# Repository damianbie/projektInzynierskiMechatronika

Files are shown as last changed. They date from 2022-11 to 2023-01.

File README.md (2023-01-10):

# Projekt Inżynierski z Mechatroniki

## struktura katalogów

- raport - raport projektu
- algorytm - implementacją algorytmu A i środowiska testowewgo
- robot - projekt fizycznego rogota
    - cady - proejkt cad robota
    - pcbV2 - projekt płytki w programie kiCad
    - soft - oprogramowanie robota napisane w C++ i IDF4.4

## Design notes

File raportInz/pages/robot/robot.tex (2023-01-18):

\section{Projekt robota}
\subsection{Założenia projektowe}
Wykonany robot powinien być jak najmniejszy i najprostszy w wykonaniu oraz sterowaniu tak aby móc przetestować przy jego pomocy działanie algorytmu A*. 
Robot będzie zbudowany z platformy, do której zostaną przyczepione napędy, elektronika sterująca oraz bateria. 
Do platformy zostaną przymocowane dwa gotowe moduły napędowe składające się z silnika, przekładni oraz dużego koła. 
Aby pojazd stał stabilnie, doczepione zostanie trzecie koło obracające się swobodnie w każdym kierunku.
Całość będzie sterowana przy pomocy mikroprocesora ESP32 oraz dwukanałowego sterownika silników DC opartym na układzie L298n.
Za zasilanie będzie odpowiadał litowo-jonowy akumulator 4S.

\subsection{Projektowanie robota w środowisku CAD}
Podstawa robota utrzymująca wszystkie komponenty zostanie wydrukowana na drukarce 3D, a
model platformy i pozostałych posiadanych elementów został wykonany w programie Fusion 360.
Wykonane modele modułów napędowych, przedniego kółka oraz baterii pozwoliły na optymalne rozmieszczenie wszystkich elementów.

\begin{figure}[H]
	\centering
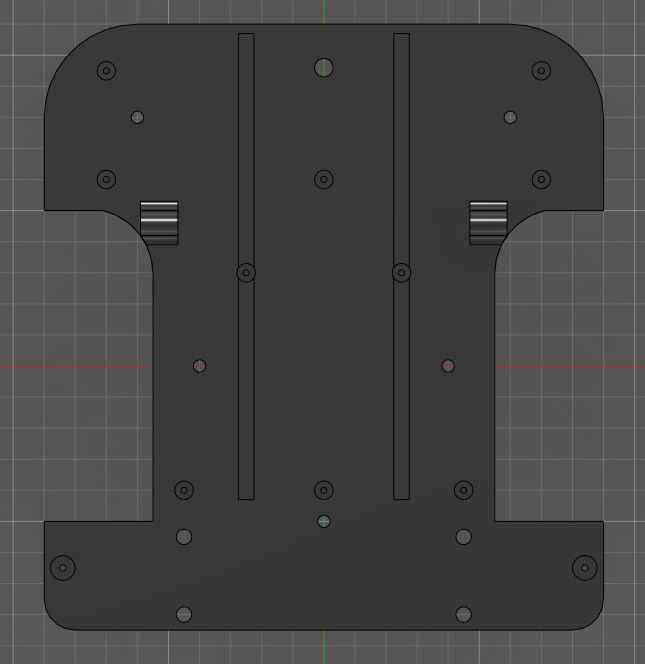
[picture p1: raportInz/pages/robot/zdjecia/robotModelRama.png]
	
	\caption{Widok z góry na podwozie robota}
	\label{Fig:robotModelRama}
\end{figure}

Model został przygotowany w programie Ultimaker Cura i wydrukowany z filamentu PLA.
Temperatur głowicy wynosiła 220$ ^\circ C$ a stołu 60$ ^\circ C$. Aby przyśpieszyć wydruk, wysokość warstwy została ustawiona na 0,2mm. 
Żeby zwiększyć wytrzymałość i lepiej zgrzać warstwy, temperatura głowicy została lekko zawyżona względem wymagań producenta filamentu,
a model posiada dwa dodatkowe wsporniki wzdłuż platformy.

\begin{figure}[H]
	\centering
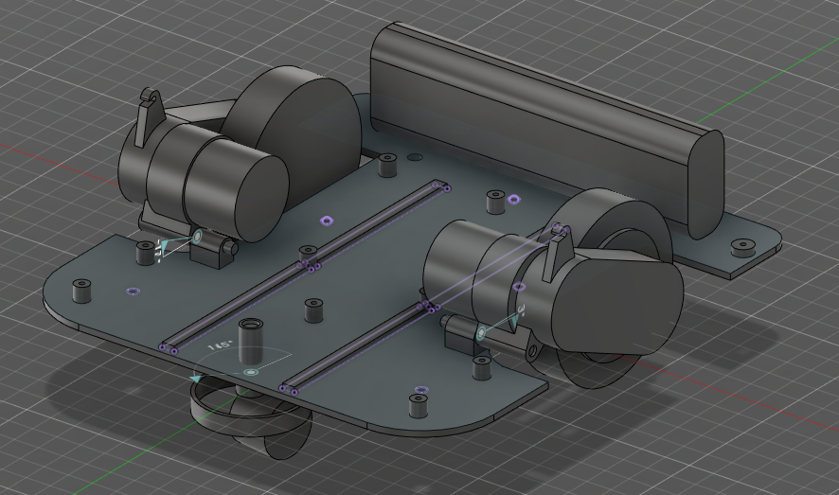
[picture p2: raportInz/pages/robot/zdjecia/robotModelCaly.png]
	
	\caption{Model robota z modułami}
	\label{fig:robotModelCaly}
\end{figure}

Na powyższym zdjęciu widać zaprojektowaną ramę wraz z odpowiednio ustawionymi gotowymi modułami. 
Moduły napędowe zaczepione są przy pomocy fabrycznego trzpienia wciskanego w ramę. 
Takie rozwiązanie oznacza że napęd może obracać się w wokół własnej osi. Aby zapewnić stały i równomierny docisk koła do podłoża,
napęd został połączony sprężyną z ramą. 

\subsection{Elektronika sterująca robotem}
Do bezprzewodowego sterowania robotem zostanie wykorzystany moduł ESP32, dla którego zostanie przygotowana odpowiednia płytka 
z wyprowadzeniami do enkoderów silnika oraz ich sterownika. Schemat i projekt płytki drukowanej został wykonany w programie KiCad. 
\begin{figure}[H]
	\centering
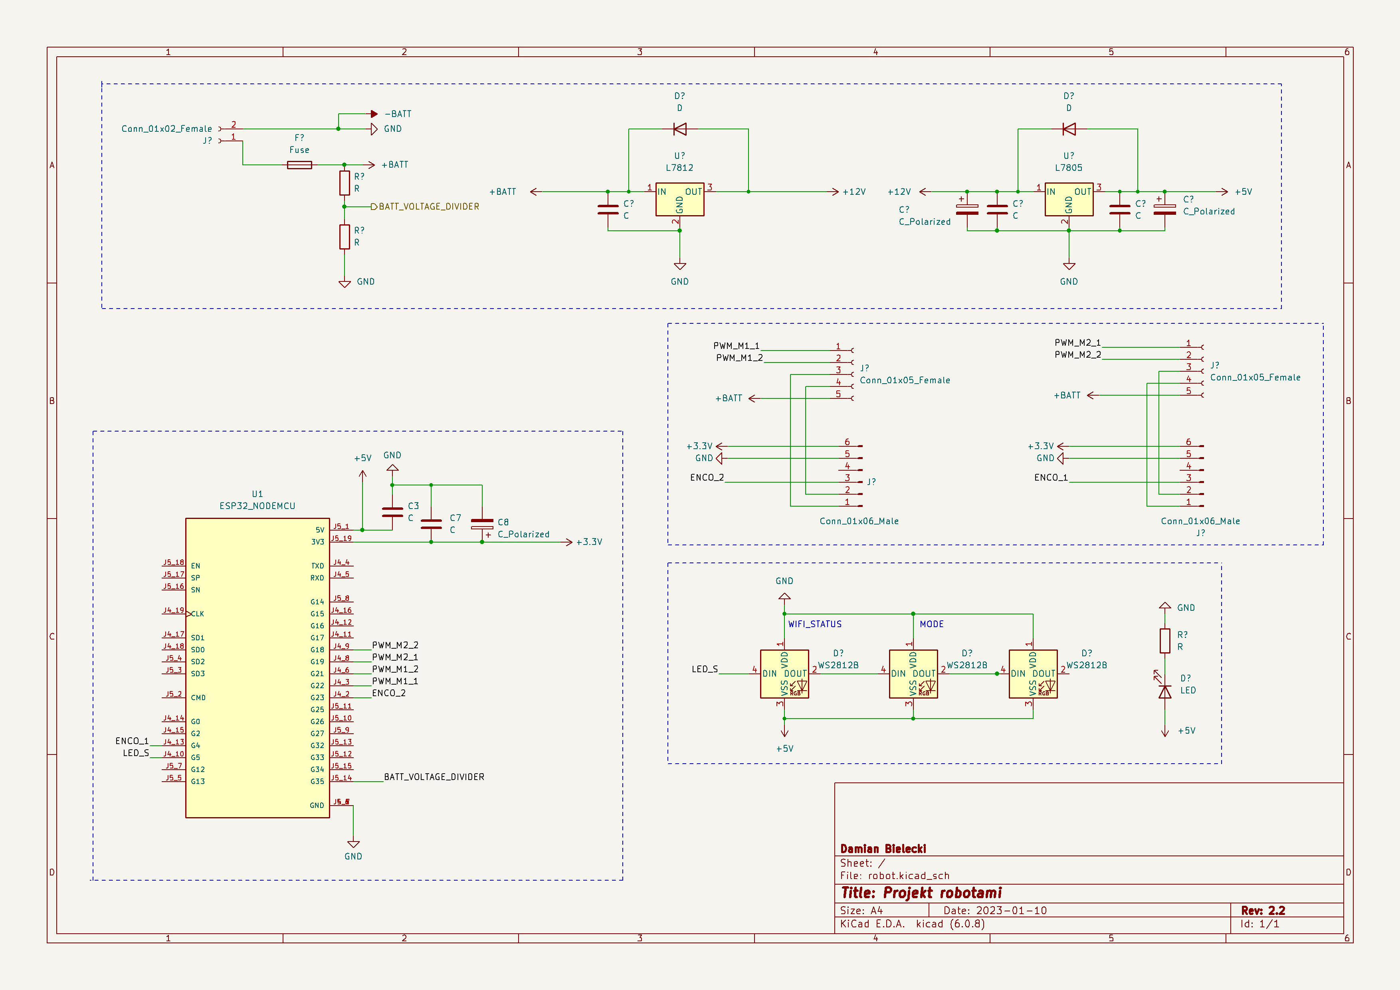
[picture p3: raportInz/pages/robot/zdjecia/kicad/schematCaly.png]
	
	\caption{Schemat połączeń pomiędzy modułami}
	\label{Fig:schematKiCad}
\end{figure}

Przedstawiony powyżej schemat został podzielony na kilka sekcji. 
Najbardziej rozbudowana jest sekcja zasilania, która poprzez dwa stabilizatory liniowe obniża napięcie z 16,8V do 5V. Mikroprocesor zasilany jest
napięciem 3,3V przygotowanym przez układ wlutowany na płytce deweloperskiej. Każda linia zasilania filtrowana jest przez kondensator elektrolityczny 
i ceramiczny, wynika to z dużego poboru prądu podczas komunikacji z WiFi. 

Kolejny segment zawiera po dwa złącza na silnik. Pierwsze złącze służy do połączenia z silnikiem, zasilania i odbierania danych z enkodera.
Drugie złącze służy do połączenia sterownika z silnikiem i dwoma kanałami PWM, pozwalającymi na płynne sterowanie kierunkiem i prędkością obrotową silnika.

Trzeci segment zawiera świecące diody programowalne służące do sygnalizacji stanu robota. Zaletą wykorzystanych tych diod jest szeregowe połączenie 
i bezpośrednie zasilanie z lini 5V. Ostatnia podłączona dioda jest na stałe i sygnalizuje podłączoną baterię.

Ostatnia sekcja, to połączenia pomiędzy modułem deweloperskim ESP32 a resztą układu. Mikroprocesor pracuje w logice 3,3V a sterownik silników 5V. 
Mimo tego, nie są potrzebne żadne układy zamieniające poziomy napięć. 
Dodatkowo obok wyprowadzeń modułu widać dodatkowe kondensatory filtrujące zasilanie. 
 
Użyte moduły napędowe posiadają enkoder inkrementalny zbudowany z czujnika halla i tarczy magnetycznej zamocowanej na wale silnika.
Silniki sterowane są modułem z układem L298n, a prędkość ustalana jest poprzez odpowiednio generowany sygnał PWM.
\begin{figure}[H]
	\centering
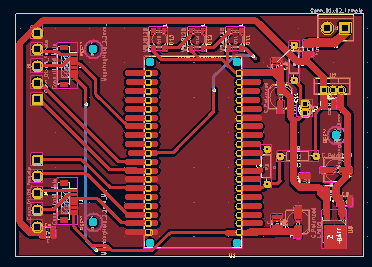
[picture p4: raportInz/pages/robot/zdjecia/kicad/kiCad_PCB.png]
	
	\caption{Projekt PCB}
	\label{Fig:kiCadPCB}
\end{figure}

Na widocznym powyżej zdjęciu widać ostateczną wersje płytki drukowanej. Większość połączeń na płytce zrealizowana jest poprzez górną warstwę miedzi,
jednak widać kilka ścieżek w dolnej warstwie.

\begin{figure}[H]
	\centering
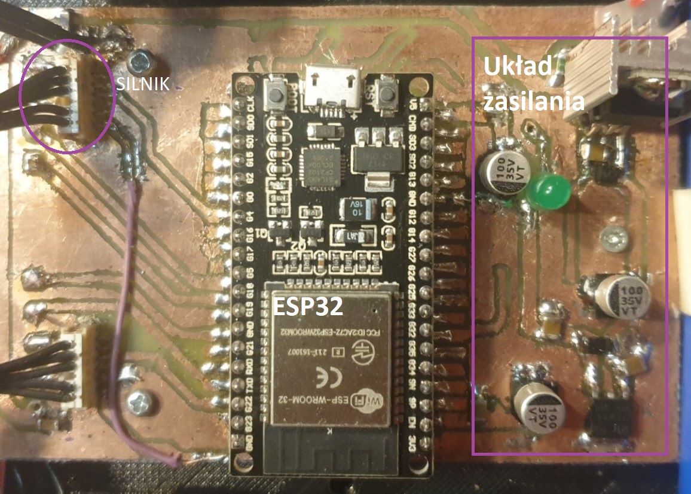
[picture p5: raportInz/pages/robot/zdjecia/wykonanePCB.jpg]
	
	\caption{Wykonana płytka}
	\label{Fig:wykonanePCB}
\end{figure}

Płytka została wykonana na jednostronnym laminacie poprzez naniesienie utwardzalnej światłem UV maski. Pozostała nie utwardzona część maski 
została zmyta w roztworze węglanu sodu. Tak przygotowana płytka została wytrawiona w 40\% roztworze chlorku żelaza(|||). 
Połączenia na dolnej warstwie zostały wykonane przy pomocy dodatkowych kabli. 

\begin{figure}[H]
	\centering
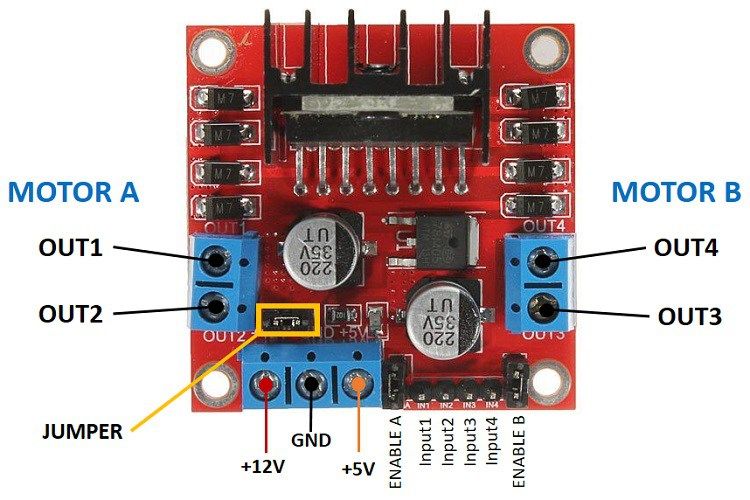
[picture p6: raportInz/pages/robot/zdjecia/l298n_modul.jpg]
	
	\caption{Wykorzystany moduł do sterowania silnikami}
	\label{Fig:modulL298}
\end{figure}

Wykonana płytka połączona jest z zewnętrznym dwukanałowym sterownikiem silników opartym na układzie L298n. 
Sterownik maksymalnie może obsłużyć silniki do 46V i 2A. Jego dużą zaletą jest praca w 5V logice
oraz zabezpieczenie przed niedozwolonymi stanami i nadmierną temperaturą. 

\subsection{Oprogramowanie robota}

Program sterujący robotem został napisany w C++,
a szkielet aplikacji bazuje na projekcie utworzonym przez framework IDF w wersji 4.4 udostępnionym 
przez producenta użytego procesora. Po za tym użyta została biblioteka implementująca 
system czasu rzeczywistego FreeRTOS i ASIO do obsługi połączenia TCP. 
\begin{figure}[H]
	\centering
	
	\caption{Schemat programu cz.1 }
	\label{Fig:Rysunek}
\end{figure}
\begin{figure}[H]
	\centering
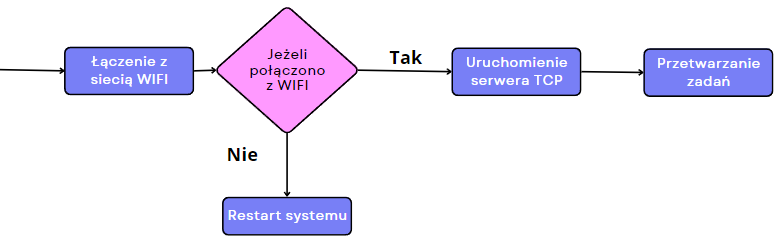
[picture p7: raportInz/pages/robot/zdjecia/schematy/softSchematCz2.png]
	
	\caption{Schemat programu cz.2}
	\label{Fig:Rysunek}
\end{figure}

Działanie programu rozpoczyna się od wywołania funkcji app\_main, inicjalizacji funkcji systemowych i sterowników silników.
W dalszej kolejności nawiązywana jest łączność z siecią WiFi. W przypadku braku połączenia system resetuje się. 
Po poprawnym połączeniu uruchamiany jest kontekst biblioteki ASIO, a następnie uruchomienie serwera TCP.
Klienci po połączeniu do utworzonego serwera wysyłają komendy tekstowe wraz z odpowiednimi argumentami, które
robot odpowiednio przetwarza. 

\subsubsection{Sterowanie silnikami}
Sterowanie silnikami odbywa się poprzez klasę MotorController, która dziedziczy po klasie PIDController implementującej regulator PID.
Obiekt automatycznie tworzy timer uruchamiający co 100ms metodę aktualizującą wyjścia sterujące silnikiem. 
Aktualna prędkość wyznaczana jest na podstawie przerwania wyzwalanego przez enkoder silnika. Przerwanie inkrementuje licznik, 
czyszczony przez wcześniej opisany timer. Nastawy regulatora PID zostały dobrane eksperymentalnie, człon proporcjonalny wynosi 8 a całkujący i różniczkujący 0,1. 
Regulator PID możemy opisać przy pomocy wzoru:

\begin{equation}
	u(x) = e(x) * P + \int{e(x)} * I + \partial{e(x)} * D 
	\label{Eq:PID}
\end{equation}
Gdzie: $e(x)$ -- jest błędem; P,I,D -- to stałe odpowiednio członu proporcjonalnego, całkującego i różniczkującego

\begin{equation}
	e(x) = y_{nast}(x) - y_{aktu}(x)
	\label{Eq:blad}
\end{equation}
Gdzie: $y_{nast}(x)$ -- to nastawa regulatora, $y_{aktu}(x)$ -- jest rzeczywistą zmierzoną wartością
 
Powyżej przedstawiony regulator został zaimplementowany w funkcji calcOutput klasy PIDController.

\begin{lstlisting}[language=C++,caption=Zaimplementowany w C++ regulator PID,label={kodCPPPIDOutput}]
float PIDController::calcOutput(float current, float set)
{
	float error = set - current;
	float der = (error - this->_lastValue)/(_timeStep* 0.001);
	
	float output =  (this->_p * error) + 
					(this->_i * error * this->_timeStep * 0.001) + 
					(this->_d * der);

	this->_lastValue = error;
	return output;
}
\end{lstlisting}

Do wyznaczenia części różniczkującej potrzebna jest wartość błędu z poprzedniego wywołania pętli, a ta zapisywana jest do zmiennej prywatnej klasy lastValue. 
Całkowanie zrealizowane jest poprzez pomnożenie przez krok dyskretyzacji. Stałe regulatora ustawiane są poprzez wywołanie konstruktora klasy.

Tak zaimplementowany regulator używany jest do wyznaczenia sygnału PWM, bezpośredniego sterującego układem L298n a ten silnikami. 

\begin{lstlisting}[language=C++,caption=Wyznaczenie modulacji PWM,label={kodCPPPWM}]
if(abs(setSpeed) - 1 > 0)
{
	pidToPwm = (int) this->calcOutput(abs(this->getCalculatedEngineRadialSpeed()), abs(setSpeed));
	if(setSpeed < 0)
	{
		pwmCh = 1;
	}
	else
		pwmCh = 0;

	pidToPwm += ledc_get_duty(LEDC_LOW_SPEED_MODE, this->_chanels[pwmCh]);
	pidToPwm = std::min(pidToPwm, 8192);
	pidToPwm = std::max(pidToPwm, 0);
}

// ustawienie wyjsc
ledc_set_duty(LEDC_LOW_SPEED_MODE, this->_chanels[pwmCh], (int)pidToPwm);
ledc_update_duty(LEDC_LOW_SPEED_MODE, this->_chanels[pwmCh]);

// ustawienie drugiego kanalu
ledc_set_duty(LEDC_LOW_SPEED_MODE, this->_chanels[(pwmCh==0)?1:0], 0);
ledc_update_duty(LEDC_LOW_SPEED_MODE, this->_chanels[(pwmCh==0)?1:0]);
\end{lstlisting}

W pierwszej kolejności sprawdzana jest zadana prędkość, jeżeli ta jest zbyt niska to na piny wystawiane są bezpośrednio stany niskie.
Jeżeli ustawiona prędkość jest poprawna to wyznaczamy wyjście regulatora. Sterowanie kierunkiem obrotów odbywa 
się poprzez znak zadanej prędkości a więc regulator otrzymuje wartości bezwzględne. 
Wyjście regulatora PID sumowane jest z aktualną nastawą. Wyjścia pwm skonfigurowane są z częstotliwością 5kHz i rozdzielczością 13bitów. 
Przed wysłaniem nastaw do kontrolera pwm, te są obcinane do obsługiwanych zakresów (tj. 0 - 8192).

\subsubsection{Serwer TCP}

Po podłączeniu zasilania i uruchomieniu systemu robot oczekuje na polecenia wysłane do robota poprzez protokół internetowy TCP. Serwer został napisany w oparciu o bibliotekę ASIO, pozwalającą na asynchroniczną obsługę wejścia i wyjścia (w tym sieci).
\begin{figure}[H]
	\centering
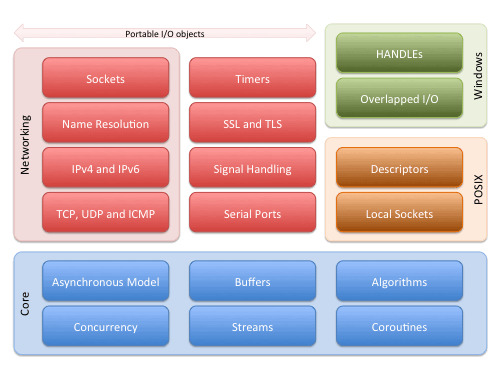
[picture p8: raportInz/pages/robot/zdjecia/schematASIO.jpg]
	
	\caption{Schemat biblioteki ASIO \cite{asio}}
	\label{Fig:schematASIO}
\end{figure}
Biblioteka została napisana w C++ i pracuje w oparciu o standard POSIX wspierany również przez wykorzystywane ESP32.
Do akceptacji przychodzących połączeń została napisana klasa Server. Konstruktor przyjmuję referencje do kontekstu utworzonego w funkcji głównej programu. 
Uruchomienie kontekstu jest ważną częścią biblioteki ASIO, przetwarzane są w niej wszystkie asynchroniczne operacje.
Aby zapewnić jak najlepszy czas przetwarzania, kontekst uruchomiony jest w oddzielnym wątku przyłączonym do drugiego fizycznego rdzenia.

\begin{figure}[H]
	\centering
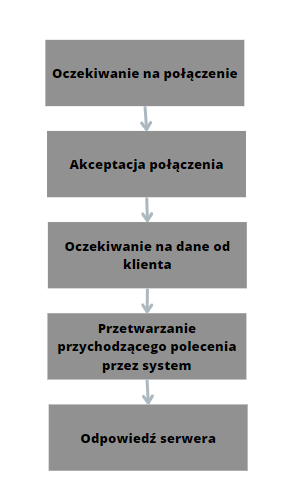
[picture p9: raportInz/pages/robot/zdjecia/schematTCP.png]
	
	\caption{Schemat działania serwera TCP}
	\label{Fig:schematSerweraTCP}
\end{figure}

Po zaakceptowaniu przychodzącego połączenia, obiekt połączenia dodawany jest do specjalnej tablicy przechowującej wszystkich klientów. 
Dane mogą być równocześnie przetwarzane w kilku miejscach a więc używane są dzielone wskaźniki, które automatycznie usuwają dane jeżeli nikt z nich nie korzysta.
Na każdym aktywnym połączeniu prowadzony jest nasłuch, dzięki czemu możemy mieć równocześnie podłączony program do generowania ścieżki i drugi pozwalający na podgląd parametrów robota.
Klient wysyła polecenia w formie tekstowej, te przekazywane są do klasy systemowej odpowiednio interpretujące ich przeznaczenie.
Jeżeli komenda tego wymaga (np. zwrócenie prędkości obrotowej silników) to dane są odsyłane do klienta w postaci tekstu i oddzielonych przerwą liczb. 

Należy pamiętać że podczas testowania i łączenia z różnymi sieciami, serwer dhcp będzie przydzielał różne adresy ip i należy to uwzględnić w programie łączącym się z robotem.

\textbf{Wykonany robot}

Poniżej widać zbudowanego i uruchomionego robota. Na zdjęciu możemy zauważyć że napęd został przyczepiony przy pomocy gumek, ponieważ 
oryginalne sprężyny tworzyły zbyt dużą siłę i robot stał krzywo. 

\begin{figure}[H]
	\centering
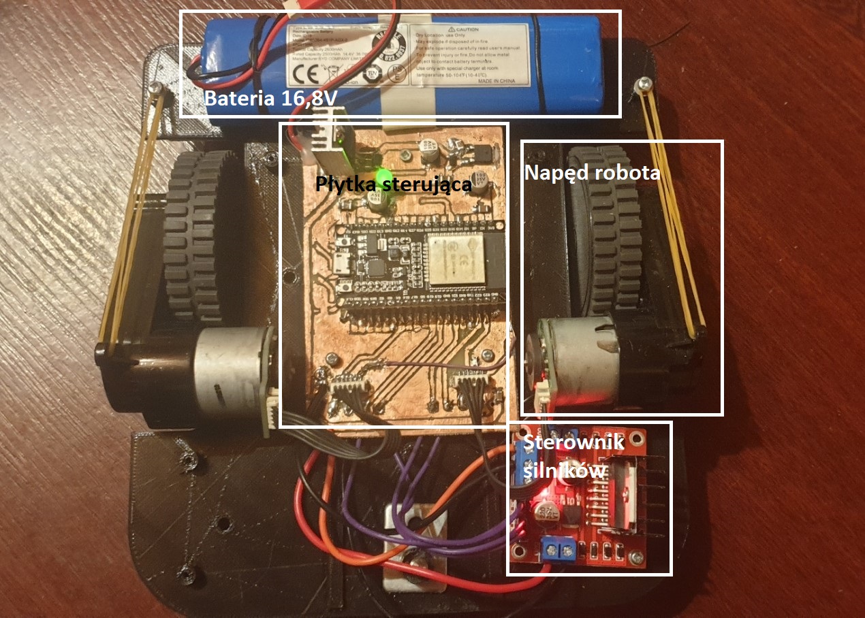
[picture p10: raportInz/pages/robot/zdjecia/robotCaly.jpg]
	
	\caption{Zbudowany robot}
	\label{Fig:zbudowanyRobot}
\end{figure}

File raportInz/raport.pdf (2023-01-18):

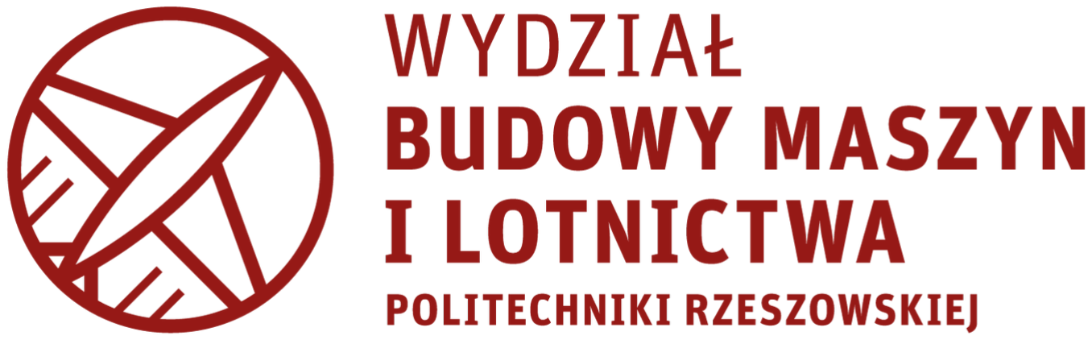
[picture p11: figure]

## Damian Bielecki

## Implementacja sterowania hierarchicznego mobilnym robotem kołowym z wykorzystaniem języka Python

## Praca dyplomowa inżynierska

## Opiekun pracy: dr inż. Paweł Penar

## Rzeszów, 2023

## Spis treści

## 1. Wprowadzenie

Od lat można zauważyć zwiększająca się popularność różnych robotów, które bazując na

wprowadzonej do systemu mapie autonomicznie poruszają się po terenie tak aby osiągnąć okre-

ślony cel. Celem projektu inżynierskiego będzie zaimplementowanie algorytmu wyszukującym

najkrótszą ścieżkę. Do przetestowania algorytmu zostanie napisany prosty program symulu-

jący robota poruszającego się po wyznaczonej ścieżce. Kolejnym etap projektu to zbudowanie

robota mającego zweryfikować zaproponowaną przez algorytm ścieżkę.

Głównym powodem podjęcia się implementacji takiego algorytmu jest chęć zapoznania

się z systemami planującymi ruch robota i próba zaimplementowania takiego rozwiązania na

fizycznym robocie.

Ze względu na cel projektu inżynierskiego oraz powód jego realizacji, przyjęto, że praca

będzie złożona z przeglądu literatury, implementacji i symulacji algorytmu A* w języku Python

oraz weryfikacji przyjętych rozwiązań obiekcie rzeczywistym.

Mając na uwadze zakres pracy, jej treść podzielono na szereg rozdziałów. Rozdział

pierwszy stanowi przegląd literatury oraz istniejących rozwiązań, które będą podstawą założeń

przyjętych we opracowywanym rozwiązaniu. Rozdział drugi skupia się na genezie, charakte-

rystyce i opisie działania wybranego algorytmu wyszukiwania najkrótszej ścieżki. Dodatkowo

zostaną przedstawione inne algorytmy zwiększającą autonomie robota mobilnego. Rozdział

trzeci przedstawia własną implementacje algorytmu A* oraz środowisko symulacyjne w języku

Python. Kolejny rozdział to omówienie budowy robota mobilnego oraz jego programu sterują-

cego. W tym kontekście szczególną uwagę poświęcono komunikacji oraz sterowaniu silnikami

Rozdział piąty stanowi podsumowanie pracy i przedstawia przeprowadzone testy wykonane w

środowisku symulacyjnym oraz rzeczywistym.

## 2. Przegląd literatury

### 2.1. Przegląd istniejących rozwiązań

Przeglądając dostępną literature opisującą algorytmy wyszukiwania najkrótszej ścieżki

możemy zauważyć pewien nie jawny podział. Pierwsza grupa artykułów skupia się na imple-

mentacji algorytmu, sprawdzeniu różnych funkcji heurestycznej i porównaniu szybkości wy-

znaczania trasy w zależności od liczby węzłów w mapie. Druga grupa artykułów przedstawia

bardziej ogólne zastosowania algorytmów takich jak A* w różnych dziedzinach przemysłu.

Pierwszy artykuł pt. "Path planning with modified A star algorithm for a mobile

robot"[1] przedstawia różne algorytmy do planowania ścieżki mobilnego robota, ich implemen-

tacje oraz przeprowadzone eksperymenty. Autorzy zwracają uwagę na to że roboty przede

wszystkim pracują wewnątrz budynków i mogą być zmuszone do budowania mapy środowiska

w trackie pracy przy pomocy metod SLAM. Do dynamicznej orientacji i generowania mapy

można wykorzystać istniejące projekty takie jak openSLAM[2] lub HectorSLAM[3] używanym

przez ROS. Jeżeli robot nie posiada żadnej mapy środowiska to musi bazować tylko i wyłącznie

na swoich wewnętrznych czujnikach co nazywa się nawigacją reaktywną. Do oceny algorytmów

wykorzystano kryteria takie jak: czas obliczeń, długość wygenerowanej ścieżki, liczbę odwie-

dzonych wierzchołków i symetrię badanego środowiska. Eksperymenty zostały przeprowadzone

w rzeczywistym środowisku i mapie wygenerowanej przez laserowy lidar robota przy pomocy

wcześniej wspomnianych metod SLAM. Z pierwszego podsumowania wynika że najlepszym

algorytmem jest JPS(A*), który jest najszybszy i odwiedził najmniej niepotrzebnych wierz-

chołków. Drugi najlepszy wynik miał 10x dłuższy czas wykonania i dotyczył niezmodyfikowa-

nej wersji algorytmu A*. Podsumowując wyniki eksperymentów najszybszym algorytmem był

JPS(A*) jednak ten wyznaczał dłuższe ścieżki. Autorzy zwracają uwagę że wybór algorytmu

zależy od tego czy wymagany jest mały czas obliczeń czy najkrótsza wyznaczona ścieżka.

Spora część artykułów skupia się na zaletach i potencjalnych różnych zastosowaniach

algorytmu A*. Jednym z nieoczywistych zastosowań wskazanych w analizowanych artykułach

jest przyśpieszenie analizy składniowej bez kontekstowych gramatyk probabilistycznych. W

przeciwieństwie do niektórych metod PCFG, algorytm A* zawsze zwróci drzewo o maksymal-

nym możliwym prawdopodobieństwie. [4]

Ponad to algorytm A* jest bardzo popularny w różnego rodzaju literaturze dotyczą-

cej gier komputerowych i sztucznej inteligencji. Dzięki niemu możemy w dosyć prosty sposób

określić ruch sztucznych obiektów w budowanej grze a dzięki prostocie i szybkości działania, algorytm nie będzie powodował dużego narzutu obliczeniowego na pozostały proces programu[5].

Ze względu na prostotę, jest często wykorzystywany w urządzeniach IOT, które mają

szczególne wymagania co do niskiego zużycia energi a więc cechują się niskimi osiągami pro-

cesora. Algorytm wykorzystywany jest między innymi w protokołach wyznaczających kolejne

routery w sieciach komputerowych[6]. Jednym z takich protokołów jest RIP, który wyznacza

trasę na podstawie wektora odległości.

### 2.2. Opis przyjętego rozwiązania

Algorytm wyznaczania najkrótszej ścieżki wraz z środowiskiem testowym został napi-

sany w języku Python. Implementacja algorytmu nie wymaga żadnych dodatkowych biblio-

tek. Do zbudowania środowiska symulacyjnego zostały użyte biblioteki graficzne do rysowania

kształtów geometrycznych oraz podstawowych elementów graficznego interfejsu użytkownika.

Weryfikacja działania algorytmu została przeprowadzona na zbudowanym trójkołowym robocie.

Oprogramowanie robota zostało napisane w języku C++ i dodatkowych bibliotekach udostęp-

nionych przez producentów użytych sterowników.

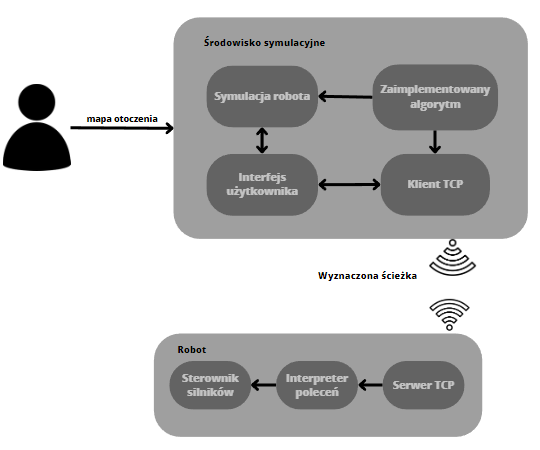
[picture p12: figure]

Rysunek 2.1: Ogólny schemat projektu

Użytkownik po uruchomieniu środowiska symulacyjnego będzie miał możliwość edycji

mapy opartej na siatce, określenia punktu początkowego i końcowego. Kolejnym krokiem jest

wyznaczenie ścieżki oraz jej graficznej reprezentacji. Tak wyznaczoną ścieżkę można wysłać do

robota operującego w środowisku rzeczywistym.

## 3. Algorytm A*

### 3.1. Geneza powstania

Algorytm A* powstał w ramach projektu Shakey, zapoczątkowanego w 1966 roku przez

Charles Rosen’a. Celem projektu było zbudowanie robota, który potrafiłby planować własne

działania. Zbudowany robot wyróżniał się na tle innych tym że integrował kilka różnych modeli

sztucznej inteligencji pracującej jako jeden system.

Robot został zbudowany z:

- kamery telewizyjnej i dalmierza optycznego - system wizyjny do obserwacji środowiska
- łącza radiowego - służącego do komunikacji z bazą, odbierania i wysyłania komend
- detektora uderzeń - pozwalający na zatrzymanie robota w przypadku kolizji

Komunikacja odbywała się poprzez wysyłane radiowo, tekstowe polecenia mające okre-

śloną strukturę np.: GOTO D4 - co oznaczało automatyczne przemieszczenie się robota do

wskazanej pozycji

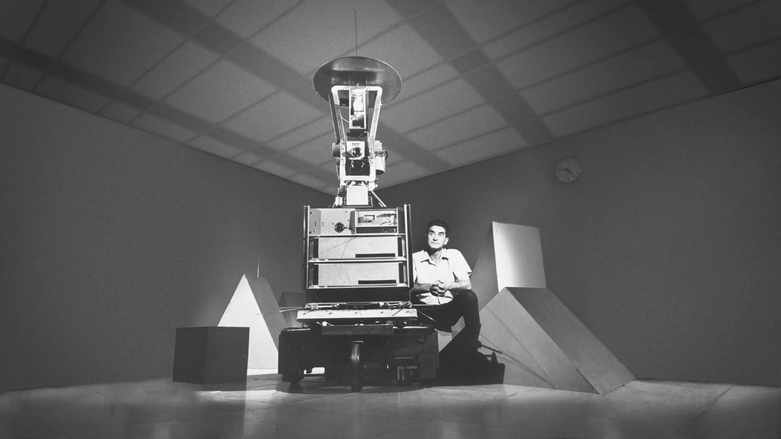
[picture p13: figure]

Rysunek 3.2: Robot Shakey i Charles Rosen, inicjator projektu [8]

### 3.2. Opis działania algorytmu

A* to heurestyczny algorytm wyznaczający najkrótszą możliwą ścieżkę w grafie. Jest to

algorytm zupełny i optymalny, a więc zawsze zostanie wyznaczone optymalne rozwiązanie. Ze względu na przeszukiwanie oparte na grafie algorytm działa najlepiej na strukturze drzewiastej.

Zadaniem algorytmu jest minimalizacja funkcji:

f(x) = h(x) +g(x) | (3.1)

gdzie: f(x) - minimalizowana funkcja, g(x) - to rzeczywisty koszt dojścia do punktu x.

Funkcja h(x) to funkcja heurestyczna, oszacowuje ona koszt dotarcia od punktu x do

wierzchołka docelowego

Zalety:

- jest kompletny i optymalny
- może przeszukiwać skomplikowane mapy
- jest najwydajniejszym takim algorytmem

Wady:

- jego wydajność w znacznej mierze zależy od funkcji heurestycznej
- Każda akcja ma stały koszt wykonania
- nie nadaje się do często zmieniającego się otoczenia robota, wymaga ponownego przeli-

czenia

Przykładowe funkcje heurestyczne:

- Funkcja euklidesowa

h(x) = K ∗

2

q
(x1 −x2)

2 + (y1 −y2)

2
(3.2)
- Geometria Manhattanu (inaczej metryka miejska)
h(x) = |x2 −x1|+|y2 −y1| | (3.3)
- Odległość oktylowa

h(x) = D1 ∗ (|x1 −x2|+|y1 −y2|) + (D2−2 ∗ D1) ∗min(|x1 −x2|,|y1 −y2|) (3.4)

Gdzie: x1 i y1 to współrzędne wyznaczanego punktu, x2 i y2 to koordynaty celu, K - oznacza

wzmocnienie, D1 - koszt skoku na wprost, D2 - koszt skoku po przekątnej

### 3.3. Analiza innych algorytmów

- RRT(Rapidly-exploring random tree)[12] - to algorytm generujący i łączący losowe

punkty w przestrzeni. Z każdym wygenerowanym wierzchołkiem sprawdzane jest czy

ten omija przeszkody. a jego działanie kończy się gdy wygenerowany węzeł jest we

wskazanym regionie lub zostanie osiągnięty limit. Jego zalety to:

- Balans pomiędzy zachłannością a eksploracją
- prosty i szybki w implementacji
- Zbiega się z rozkładem próbkowania

wady:

- jest czuły na metrykę
- duża złożoność obliczeniowa
- SLAM(Simultaneous localization and mapping) [13] - jest metodą używaną w

autonomicznych pojazdach. Pozwana na zbudowanie oraz lokalizacje pojazdu względem

otoczenia na mapie. Algorytm ten nie wyznacza bezpośrednio ścieżki omijającej prze-

szkody jednak w praktyce jest ważnym elementem takiego systemu. Każdy ruch robota

w rzeczywistym środowisku jak i sama mapa obarczona jest pewnym błędem powodują-

cym że robot znajduje się w innym miejscu niż zakładamy. Możemy wyróżnić działanie

algorytmu w oparciu o lidary albo o metody wizyjne. Wadą metody jest wysoki koszt

obliczeniowy i narastający z czasem błąd pozycji co w konsekwencji może spowodować

utratę pozycji.

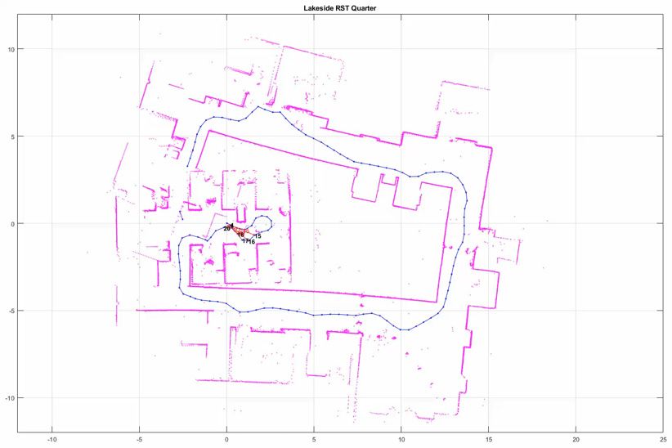
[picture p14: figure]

Rysunek 3.3: Przykład mapowania metodą SLAM[13]

## 4. Implementacja

### 4.1. Implementacja algorytmu

Mechanizm wyszukiwania najkrótszej ścieżki został zamknięty w jednym module o na-

zwie aStar. Na moduł składa się klasa AStar ze wszystkimi potrzebnymi metodami oraz do-

datkowa klasa Node reprezentująca pojedynczy punkt przeszukiwanego grafu.

Wyznaczanie najkrótszej ścieżki rozpoczyna się od wyznaczenia kosztu punktu starto-

wego i utworzenia zbioru z nieprzeszukanymi wierzchołkami, do którego dopisujemy punkt

początkowy.

1 | openList = []
2 | startNode . h = self . heurestic ( startNode . getCords () , endNode . getCords
() )
3 | startNode . g = 0
4 | heappush ( openList , startNode )

Listing 1: Przygotowanie danych

Wewnętrzna funkcja heurestic przyjmująca pozycje dwóch punktów odpowiada za wyli-

czenie optymistycznego kosztu przejścia od punktu x do wierzchołka docelowego. Takie podej-

ście pozwala na szybką podmianę funkcji bez znaczących zmian w programie. Wykorzystywana

funkcja heurestyczna to równanie nr. (3.2)

W kolejnym kroku uruchamiana jest pętla, która wykonywana jest dopóki w zbiorze

otwartym znajdują się nie odwiedzone elementy. Z listy pobierany jest element o najmniejszej

liczbie punktów co oznacza, że dany wierzchołek drzewa ma największe szanse być najlepszym

rozwiązaniem. Jeżeli pobrany element nie jest celem to dalej pobierani i przetwarzani są wszy-

scy jego sąsiedzi. W tym rozwiązaniu, dla zaoszczędzenia pamięci, symulator przechowuję tylko

przeszkody. W związku z tym do pobrania sąsiadów używana jest specjalna funkcja sprawdza-

jąca czy na mapie o wskazanych koordynatach istnieje punkt. Jeżeli takowy obiekt nie istnieje

to oznacza, że algorytm może użyć tych współrzędnych do trasowania ścieżki. Od tej części

programu zależy, czy algorytm ma wyznaczyć ścieżkę uwzględniając skoki po skosie.

1 | neighborNode = self . _findNodeOnList ( openList , newCords )
2 | if neighborNode is None :
3 | neighborNode = Node ( newCords )
4 | neighborNode . g = COST
5 | neighborNode . h = self . heurestic ( newCords , endNode . getCords () )
6 | neighborNode . parent = currentNode
7 | openList . append ( neighborNode )

8
9 | distance_from_curr_to_neighbor = COST
10 | scoreFromStartToCurrentNeighbor = | currentNode . g +
| distance_from_curr_to_neighbor

12 | if neighborNode . getScore () <= currentNode . getScore () :
13 | neighborNode . g = scoreFromStartToCurrentNeighbor
14 | neighborNode . h = scoreFromStartToCurrentNeighbor + self . heurestic (
| newCords , endNode . getCords () )
15 | neighborNode . parent = currentNode

Listing 2: Wyznaczenie kosztu ścieżki

Powyższy kod odpowiada za wyznaczenie kosztu przejścia do sąsiada. Jeżeli punkt nie

istnieje jeszcze w otwartym zbiorze to jest tworzony i do niego dodawany. Zgodnie z założeniem

całkowity koszt to suma rzeczywistego kosztu dystansu i wyniku funkcji heurestycznej. Rze-

czywisty koszt (funkcja g(x)) jest ustalony na sztywno i zależy od współrzędnych, do których

skaczemy. Jeżeli następny punkt jest na wprost to koszt wynosi 10. Jako iż przechodzimy po

siatce z węzłami o stałej i równej odległości to koszt skoku do sąsiada po skosie został wyzna-

czony z twierdzenia Pitagorasa. Należy zwrócić uwagę, że jeżeli całkowity koszt jest mniejszy

od aktualnego to węzeł ma ustawianego rodzica, ma to duże znaczenie w przypadku wyjścia z

pętli i wyznaczenia najkrótszej trasy spośród wszystkich kosztów.

1 | if currentNode == endNode :
2 | path = []
3 | while currentNode is not None :
4 | path . append ( currentNode )
5 | currentNode = currentNode . getParent ()
6 | return path
7 | else :
8 | return []

Listing 3: Przygotowanie danych

Po zakończeniu pętli, sprawdzane jest czy została znaleziona ścieżka, jeżeli takowa ist-

nieje to w kolejnej pętli wyznaczane są przy pomocy pola wskazującego na rodzica kolejne

punkty trasy. Jeżeli węzeł nie jest punktem końcowym to trasa nie została znaleziona i zwra-

cana jest pusta lista.

### 4.2. Implementacja środowiska testowego

Środowisko symulacyjne zostało napisane w języku Python i bibliotekach pygame[9] i

pygame_gui[10], zapewniających obsługę graficznego interfejsu użytkownika.

1 | if __name__ == ’__main__ ’:
2 | app = App ()
3 | app . main ()

Listing 4: Uruchomienie aplikacji

Obsługa mapy

Dla logicznego podzielenia programu została napisana główna klasa programu o nazwie

App. Takie podejście pozwoliło na odseparowanie poszczególnych funkcji aplikacji. W pierwszej

kolejności konstruktor obiektu aplikacji, generuje okno, tworzy graficzne elementy użytkownika

oraz ustawia odpowiednie flagi informujące o stanie aplikacji. Dalej wywoływana jest funkcja

main wczytująca odpowiednią mapę z pliku, a następnie uruchamiająca główną pętlę programu

działającą w 60 klatkach na sekundę.

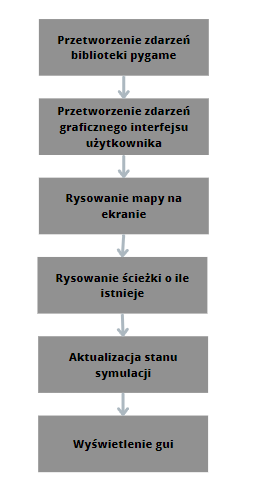
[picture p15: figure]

Rysunek 4.4: Schemat głównej pętli programu

Aby uprościć symulowanie różnych scenariuszy i rozmiarów map otoczenia, ta ładowana

jest ze wskazanego w programie pliku. Wskazany plik jest w formacie json i podzielony jest na

dwie sekcje. Pierwsza dostarcza informacji o samej mapie, natomiast druga o poruszającym się

po niej robocie. Sekcja mapy zawiera lokalizacje do pliku tekstowego z zapisanymi elementami.

1 ( self .map , self . robot ) = MapLoader . fromJson (" maps / m02 . json ")

Listing 5: Uruchomienie aplikacji

Ładowaniem wszystkich tych informacji zajmuje się specjalna metoda w klasie MapLoader,

wywołana przed uruchomieniem pętli głównej programu. Wczytywana mapa jest w postaci

siatki i każdy jej element ma stały rozmiar. Symulator rozróżnia kilka typów węzłów:

- brak elementu - możliwy przejazd
- ściana - przeszkoda do ominięcia przez algorytm
- punkt początkowy - od niego rozpoczyna się wyznaczanie ścieżki, jest zdefiniowany przez

użytkownika

- punkt końcowy - analogicznie jak w poprzednim przypadku
- ścieżka - element wyznaczonej trasy

Wszystkie wymienione typy zapisane są w klasie Tile, reprezentującej pojedynczy ry-

sowany i zapisywany w pliku kwadrat. Użytkownik może w każdej chwili działania aplikacji

edytować mapę a przed zamknięciem programu zaktualizowana mapa jest zapisywana do pliku.

Wyjątkiem jest obiekt będący elementem ścieżki, ten nie jest zapisywany do pliku, ponieważ

generowany jest dynamicznie i służy tylko do reprezentacji wygenerowanej ścieżki.

Wyznaczanie ścieżki i symulacja

Po załadowaniu program oczekuje na akcje użytkownika i ewentualne uruchomienie wy-

znaczania ścieżki lub całej symulacji.

1 | elif ev . ui_element == self . _startAStar :
2 | star = AStar ( self .map.map , self . map . getSize () )
3 | star . diagonalJump ( self . _diagonalJump )
4 | star . diagolnalCorrection ( self . _diagonalCorrextion )
5 | self . path | = star . findPath2 ( Node ( self . map . getStartCords () ) ,
Node (( self . map . getEndCords () ) ) )
6 | self . _pathExist = True
7 | self . robot . stopSimulation ()
8 | self . robot . hideRobot ()

Listing 6: Uruchomienie aplikacji

Po kliknięciu w przycisk odpowiadający za wyznaczenie i pokazanie ścieżki, program

tworzy obiekt wyznaczający trasę i ustawia dodatkowe opcje algorytmu (np. skok po przekąt-

nych). Dalej pobierana jest wyznaczona trasa będąca tablicą kolejnych punktów, po których

należy przejść aby dojść do celu. Na końcu ustawiana jest odpowiednia flaga programu, za-

trzymywana jest symulacja i ukrywany jest robot (mamy nowo wyznaczoną trasę). Przycisk

uruchamiający symulacje sprawdza czy istnieje ścieżka i w razie potrzeby ją generuje. Na-

stępnie trasa podawana jest do obiektu robota odpowiadającego za symulacje i dalej jest ona

uruchamiana.

Przejście robota po ścieżce

Symulator robota pobiera pierwszy punkt, do którego ma dotrzeć. Zmiana pozycji od-

bywa się poprzez regulator typu P z ustawioną nastawą na wskazany punkt. Wartość wzmoc-

nienia proporcjonalnego wczytana jest z pliku i oznaczona jest jako szybkość robota. Dalszy

etap to sprawdzenie czy symulowany robot dotarł do celu.

if abs ( deltaPos0 ) < 0.2 and abs ( deltaPos1 ) < 0.2:
self . _currentTarget -= 1

Listing 7: Uruchomienie aplikacji

Realizowane jest to poprzez sprawdzenie czy wartość bezwzględna z różnicy aktualnej oraz

docelowej pozycji jest mniejsza niż 0,1. Po osiągnięciu punktu, ustawiany jest nowy indeks

tablicy wskazujący na kolejny cel. Jeżeli na początku aktualizacji indeks jest ujemny to robot

przejechał po całej wyznaczonej trasie.

Komunikacja z robotem

Po wyznaczeniu ścieżki symulator na polecenie użytkownika może połączyć się ze zbudo-

wanym robotem aby ten osiągnął założony cel. Zgodnie ze schematem 2.1 robot po połączeniu

z siecią WiFi i utworzeniu serwera TCP oczekuje na wysyłane komendy. Aplikacja podczas

uruchamiania, tworzy gniazdo, które potem zostanie wykorzystane do połączenia.

1 | self . _robotSocket | = socket . socket ( socket . AF_INET , socket .
| SOCK_STREAM )

Listing 8: Utworzone gniazdo

Dla zwiększenia elastyczności utworzone zostały dwa pola tekstowe pozwalające na wprowa-

dzenie adresu ip oraz portu z uruchomionym serwerem. Po wprowadzeniu wymaganych danych

operator może spróbować nawiązać połączenie z robotem poprzez specjalny przycisk.

if self . _robotSocketFlag is True :
self . _robotSocket . close ()

print ( f" Laczenie z robotem {( self . _textRobotIp . get_text () , int( self . _textRobotPort . get_text ()))}")
self . _robotSocket . settimeout (1)
| try :
self . _robotSocket . connect (( self . _textRobotIp . get_text () , int ( self . _textRobotPort . get_text () ) ) )
self . _robotSocketFlag = True
self . _sendCommandToRobot (" setMode auto ")
print (" Podlaczono !!! ")
| except Exception as err :
self . _robotSocketFlag = False
print ( f" Blad polaczenia z robotem ")
| print ( err )

Listing 9: Nawiązanie połączenia

W pierwszej kolejności sprawdzana jest flaga informująca o stanie połączenia, jeżeli jest aktywne

to jest ono zamykane. Na utworzonym gnieździe wywoływana jest funkcja connect z wprowa-

dzonymi przez użytkownika parametrami. Cała operacja zamknięta jest w bloku try..except

a więc jeżeli program nie połączy się z robotem to wyświetlana jest odpowiednia informacja.

Podczas łączenia należy zwracać uwagę na podsieci, w których jest robot i sterujący laptop.

Dodatkowo robot posiada dynamiczne ip co zostało szerzej opisane w rozdziale o oprogramo-

waniu robota. Jeżeli żaden wyjątek nie został rzucony to wysyłana jest pierwsza komenda

ustawiająca tryb robota na automatyczny.

1 | def _sendCommandToRobot ( self , cmd ) :
2 | if self . _robotSocketFlag is False :
3 | print (" Robot nie podlaczony !!")
4 | return

5
6 | try :
7 | self . _robotSocket . send ( str . encode ( cmd ) )
8 | except OSError as err :
9 | print (" Robot nie podlaczony !!! ")
10 | self . _robotSocket . close ()
11 | self . _robotSocketFlag = False
12 | return

Listing 10: Wysyłanie komendy do robota

Program może wysłać dowolną komendę poprzez metodę sendCommandToRobot. Podobnie

jak przy połączeniu, metoda wysyłająca dane może rzucić wyjątek o braku połączenia. W

takim przypadku wyświetlana jest odpowiednia informacja i resetowana jest flaga połączenia.

Finalna wersja programu

Na poniższym zrzucie widać uruchomiony program z trwającą symulacją. Po prawej

stronie został umieszczony panel z interfejsem użytkownika. Po lewej stronie widoczna jest

wczytana mapa. Kolorem niebieskim został oznaczony punkt startowy a czerwonym końcowy.

Żółte kratki oznaczają wyznaczoną przez algorytm ścieżkę, po której przejdzie robot. Szare

pola to przeszkody, które robot ma ominąć. Robot oznaczony jest przez jasno-zielone koło,

które przesuwa się po mapie.

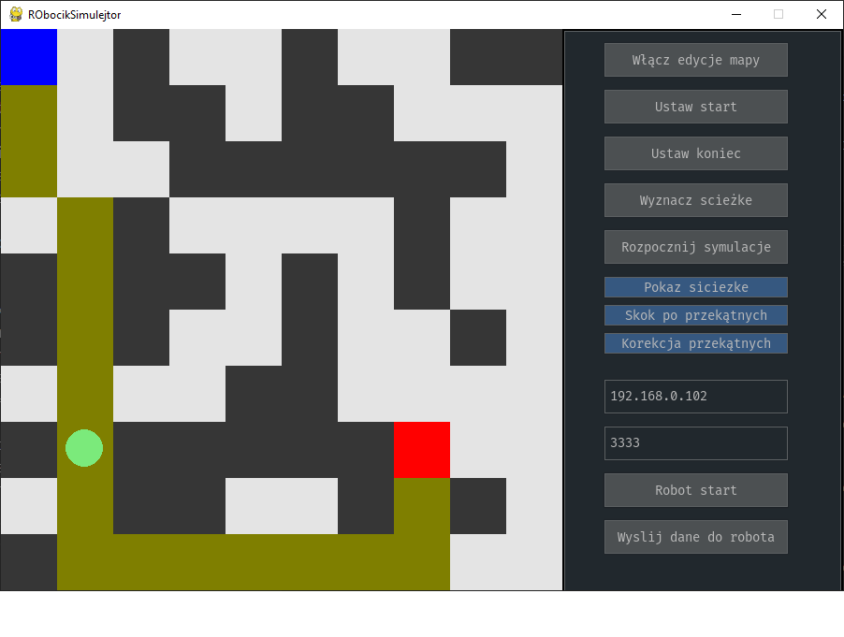
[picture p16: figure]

Rysunek 4.5: Widok finalnej wersji programu

## 5. Projekt robota

### 5.1. Założenia projektowe

Wykonany robot powinien być jak najmniejszy i najprostszy w wykonaniu oraz stero-

waniu tak aby móc przetestować przy jego pomocy działanie algorytmu A*. Robot będzie

zbudowany z platformy, do której zostaną przyczepione napędy, elektronika sterująca oraz ba-

teria. Do platformy zostaną przymocowane dwa gotowe moduły napędowe składające się z

silnika, przekładni oraz dużego koła. Aby pojazd stał stabilnie, doczepione zostanie trzecie

koło obracające się swobodnie w każdym kierunku. Całość będzie sterowana przy pomocy mi-

kroprocesora ESP32 oraz dwukanałowego sterownika silników DC opartym na układzie L298n.

Za zasilanie będzie odpowiadał litowo-jonowy akumulator 4S.

### 5.2. Projektowanie robota w środowisku CAD

Podstawa robota utrzymująca wszystkie komponenty zostanie wydrukowana na drukarce

3D, a model platformy i pozostałych posiadanych elementów został wykonany w programie

Fusion 360. Wykonane modele modułów napędowych, przedniego kółka oraz baterii pozwoliły

na optymalne rozmieszczenie wszystkich elementów.


Rysunek 5.6: Widok z góry na podwozie robota

Model został przygotowany w programie Ultimaker Cura i wydrukowany z filamentu

PLA. Temperatur głowicy wynosiła 220◦C a stołu 60◦C. Aby przyśpieszyć wydruk, wysokość

warstwy została ustawiona na 0,2mm. Żeby zwiększyć wytrzymałość i lepiej zgrzać warstwy, temperatura głowicy została lekko zawyżona względem wymagań producenta filamentu, a mo-

del posiada dwa dodatkowe wsporniki wzdłuż platformy.


Rysunek 5.7: Model robota z modułami

Na powyższym zdjęciu widać zaprojektowaną ramę wraz z odpowiednio ustawionymi

gotowymi modułami. Moduły napędowe zaczepione są przy pomocy fabrycznego trzpienia

wciskanego w ramę. Takie rozwiązanie oznacza że napęd może obracać się w wokół własnej osi.

Aby zapewnić stały i równomierny docisk koła do podłoża, napęd został połączony sprężyną z

ramą.

### 5.3. Elektronika sterująca robotem

Do bezprzewodowego sterowania robotem zostanie wykorzystany moduł ESP32, dla któ-

rego zostanie przygotowana odpowiednia płytka z wyprowadzeniami do enkoderów silnika oraz

ich sterownika. Schemat i projekt płytki drukowanej został wykonany w programie KiCad.


Rysunek 5.8: Schemat połączeń pomiędzy modułami

Przedstawiony powyżej schemat został podzielony na kilka sekcji. Najbardziej rozbu-

dowana jest sekcja zasilania, która poprzez dwa stabilizatory liniowe obniża napięcie z 16,8V

do 5V. Mikroprocesor zasilany jest napięciem 3,3V przygotowanym przez układ wlutowany na

płytce deweloperskiej. Każda linia zasilania filtrowana jest przez kondensator elektrolityczny i

ceramiczny, wynika to z dużego poboru prądu podczas komunikacji z WiFi.

Kolejny segment zawiera po dwa złącza na silnik. Pierwsze złącze służy do połączenia z

silnikiem, zasilania i odbierania danych z enkodera. Drugie złącze służy do połączenia sterow-

nika z silnikiem i dwoma kanałami PWM, pozwalającymi na płynne sterowanie kierunkiem i

prędkością obrotową silnika.

Trzeci segment zawiera świecące diody programowalne służące do sygnalizacji stanu

robota. Zaletą wykorzystanych tych diod jest szeregowe połączenie i bezpośrednie zasilanie z

lini 5V. Ostatnia podłączona dioda jest na stałe i sygnalizuje podłączoną baterię.

Ostatnia sekcja, to połączenia pomiędzy modułem deweloperskim ESP32 a resztą układu.

Mikroprocesor pracuje w logice 3,3V a sterownik silników 5V. Mimo tego, nie są potrzebne żadne układy zamieniające poziomy napięć. Dodatkowo obok wyprowadzeń modułu widać dodatkowe

kondensatory filtrujące zasilanie.

Użyte moduły napędowe posiadają enkoder inkrementalny zbudowany z czujnika halla

i tarczy magnetycznej zamocowanej na wale silnika. Silniki sterowane są modułem z układem

L298n, a prędkość ustalana jest poprzez odpowiednio generowany sygnał PWM.

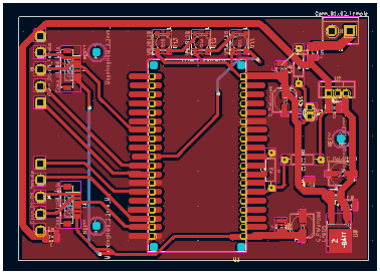
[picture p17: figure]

Rysunek 5.9: Projekt PCB

Na widocznym powyżej zdjęciu widać ostateczną wersje płytki drukowanej. Większość

połączeń na płytce zrealizowana jest poprzez górną warstwę miedzi, jednak widać kilka ścieżek

w dolnej warstwie.


Rysunek 5.10: Wykonana płytka

Płytka została wykonana na jednostronnym laminacie poprzez naniesienie utwardzalnej światłem UV maski. Pozostała nie utwardzona część maski została zmyta w roztworze wę-

glanu sodu. Tak przygotowana płytka została wytrawiona w 40% roztworze chlorku żelaza(|||).

Połączenia na dolnej warstwie zostały wykonane przy pomocy dodatkowych kabli.

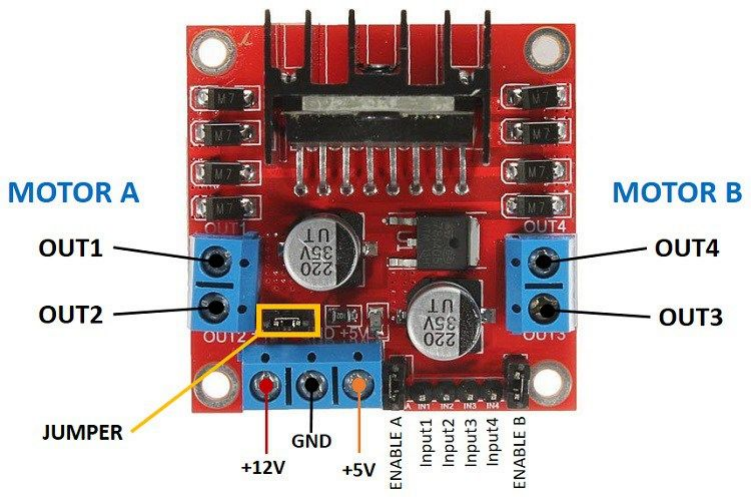
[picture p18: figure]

Rysunek 5.11: Wykorzystany moduł do sterowania silnikami

Wykonana płytka połączona jest z zewnętrznym dwukanałowym sterownikiem silników

opartym na układzie L298n. Sterownik maksymalnie może obsłużyć silniki do 46V i 2A. Jego

dużą zaletą jest praca w 5V logice oraz zabezpieczenie przed niedozwolonymi stanami i nad-

mierną temperaturą.

### 5.4. Oprogramowanie robota

Program sterujący robotem został napisany w C++, a szkielet aplikacji bazuje na pro-

jekcie utworzonym przez framework IDF w wersji 4.4 udostępnionym przez producenta użytego

procesora. Po za tym użyta została biblioteka implementująca system czasu rzeczywistego

FreeRTOS i ASIO do obsługi połączenia TCP.

Rysunek 5.12: Schemat programu cz.1

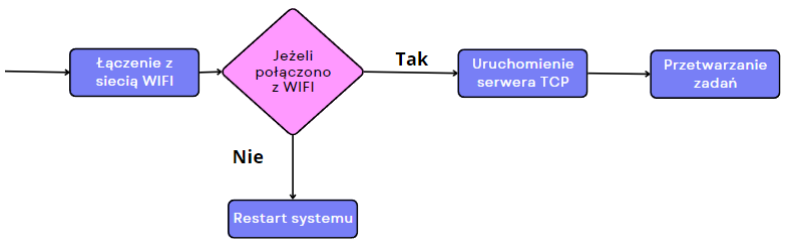
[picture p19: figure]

Rysunek 5.13: Schemat programu cz.2

Działanie programu rozpoczyna się od wywołania funkcji app_main, inicjalizacji funkcji

systemowych i sterowników silników. W dalszej kolejności nawiązywana jest łączność z siecią

WiFi. W przypadku braku połączenia system resetuje się. Po poprawnym połączeniu uru-

chamiany jest kontekst biblioteki ASIO, a następnie uruchomienie serwera TCP. Klienci po

połączeniu do utworzonego serwera wysyłają komendy tekstowe wraz z odpowiednimi argu-

mentami, które robot odpowiednio przetwarza.

### 5.4.1. Sterowanie silnikami

Sterowanie silnikami odbywa się poprzez klasę MotorController, która dziedziczy po

klasie PIDController implementującej regulator PID. Obiekt automatycznie tworzy timer uru-

chamiający co 100ms metodę aktualizującą wyjścia sterujące silnikiem. Aktualna prędkość

wyznaczana jest na podstawie przerwania wyzwalanego przez enkoder silnika. Przerwanie in-

krementuje licznik, czyszczony przez wcześniej opisany timer. Nastawy regulatora PID zostały

dobrane eksperymentalnie, człon proporcjonalny wynosi 8 a całkujący i różniczkujący 0,1. Re-

gulator PID możemy opisać przy pomocy wzoru:

u(x) = e(x) ∗P +

Z
e(x) ∗ I +∂e(x) ∗ D | (5.5)

Gdzie: e(x) – jest błędem; P,I,D – to stałe odpowiednio członu proporcjonalnego, całkującego

i różniczkującego

e(x) = ynast(x)−yaktu(x) | (5.6)

Gdzie: ynast(x) – to nastawa regulatora, yaktu(x) – jest rzeczywistą zmierzoną wartością

Powyżej przedstawiony regulator został zaimplementowany w funkcji calcOutput klasy

PIDController.

1 | float PIDController :: calcOutput ( float current , float set )
2 | {

3 | float error = set - current ;
4 | float der = ( error - this - > _lastValue ) /( _timeStep * 0.001) ;

5
6 | float output = | (this - > _p * error ) +
7 | (this -> _i * error * this - > _timeStep * 0.001) +
8 | (this -> _d * der ) ;

9
10 | this - > _lastValue = error ;
11 | return output ;
12 | }

Listing 11: Zaimplementowany w C++ regulator PID

Do wyznaczenia części różniczkującej potrzebna jest wartość błędu z poprzedniego wy-

wołania pętli, a ta zapisywana jest do zmiennej prywatnej klasy lastValue. Całkowanie zrealizo-

wane jest poprzez pomnożenie przez krok dyskretyzacji. Stałe regulatora ustawiane są poprzez

wywołanie konstruktora klasy.

Tak zaimplementowany regulator używany jest do wyznaczenia sygnału PWM, bezpo-

średniego sterującego układem L298n a ten silnikami.

1 | if( abs ( setSpeed ) - 1 > 0)
2 | {
3 | pidToPwm = ( int ) this - > calcOutput ( abs (this - >
getCalculatedEngineRadialSpeed () ) , abs ( setSpeed ) ) ;
4 | if( setSpeed < 0)
5 | {
6 | pwmCh = 1;
7 | }
8 | else
9 | pwmCh = 0;

10
11 | pidToPwm += ledc_get_duty ( LEDC_LOW_SPEED_MODE , this - > _chanels [ pwmCh ])
| ;
12 | pidToPwm = std :: min ( pidToPwm , 8192) ;
13 | pidToPwm = std :: max ( pidToPwm , 0) ;
14 | }

15
16 | // ustawienie wyjsc
17 | ledc_set_duty ( LEDC_LOW_SPEED_MODE , this - > _chanels [ pwmCh ] , (int) pidToPwm
) ;
18 ledc_update_duty ( LEDC_LOW_SPEED_MODE , this - > _chanels [ pwmCh ]) ;

19
20 | // ustawienie drugiego kanalu
21 | ledc_set_duty ( LEDC_LOW_SPEED_MODE , this - > _chanels [( pwmCh ==0) ?1:0] , 0) ;
22 | ledc_update_duty ( LEDC_LOW_SPEED_MODE , this - > _chanels [( pwmCh ==0) ?1:0]) ;

Listing 12: Wyznaczenie modulacji PWM

W pierwszej kolejności sprawdzana jest zadana prędkość, jeżeli ta jest zbyt niska to

na piny wystawiane są bezpośrednio stany niskie. Jeżeli ustawiona prędkość jest poprawna

to wyznaczamy wyjście regulatora. Sterowanie kierunkiem obrotów odbywa się poprzez znak

zadanej prędkości a więc regulator otrzymuje wartości bezwzględne. Wyjście regulatora PID sumowane jest z aktualną nastawą. Wyjścia pwm skonfigurowane są z częstotliwością 5kHz

i rozdzielczością 13bitów. Przed wysłaniem nastaw do kontrolera pwm, te są obcinane do

obsługiwanych zakresów (tj. 0 - 8192).

### 5.4.2. Serwer TCP

Po podłączeniu zasilania i uruchomieniu systemu robot oczekuje na polecenia wysłane

do robota poprzez protokół internetowy TCP. Serwer został napisany w oparciu o bibliotekę

ASIO, pozwalającą na asynchroniczną obsługę wejścia i wyjścia (w tym sieci).


Rysunek 5.14: Schemat biblioteki ASIO [11]

Biblioteka została napisana w C++ i pracuje w oparciu o standard POSIX wspierany

również przez wykorzystywane ESP32. Do akceptacji przychodzących połączeń została na-

pisana klasa Server. Konstruktor przyjmuję referencje do kontekstu utworzonego w funkcji

głównej programu. Uruchomienie kontekstu jest ważną częścią biblioteki ASIO, przetwarzane

są w niej wszystkie asynchroniczne operacje. Aby zapewnić jak najlepszy czas przetwarzania,

kontekst uruchomiony jest w oddzielnym wątku przyłączonym do drugiego fizycznego rdzenia.


Rysunek 5.15: Schemat działania serwera TCP

Po zaakceptowaniu przychodzącego połączenia, obiekt połączenia dodawany jest do spe-

cjalnej tablicy przechowującej wszystkich klientów. Dane mogą być równocześnie przetwarzane

w kilku miejscach a więc używane są dzielone wskaźniki, które automatycznie usuwają dane

jeżeli nikt z nich nie korzysta. Na każdym aktywnym połączeniu prowadzony jest nasłuch,

dzięki czemu możemy mieć równocześnie podłączony program do generowania ścieżki i drugi

pozwalający na podgląd parametrów robota. Klient wysyła polecenia w formie tekstowej, te

przekazywane są do klasy systemowej odpowiednio interpretujące ich przeznaczenie. Jeżeli

komenda tego wymaga (np. zwrócenie prędkości obrotowej silników) to dane są odsyłane do

klienta w postaci tekstu i oddzielonych przerwą liczb.

Należy pamiętać że podczas testowania i łączenia z różnymi sieciami, serwer dhcp będzie

przydzielał różne adresy ip i należy to uwzględnić w programie łączącym się z robotem.

Wykonany robot

Poniżej widać zbudowanego i uruchomionego robota. Na zdjęciu możemy zauważyć że

napęd został przyczepiony przy pomocy gumek, ponieważ oryginalne sprężyny tworzyły zbyt

dużą siłę i robot stał krzywo.


Rysunek 5.16: Zbudowany robot

## 6. Przeprowadzone testy

Do testów zostanie wykorzystana mapa o rozmiarze 35x35 bloków.

### 6.1. Wpływ ustawień na wyznaczoną ścieżkę

W pierwszym eksperymencie został włączony skok po przekątnej i korekcja wynikająca

z tego błędów.

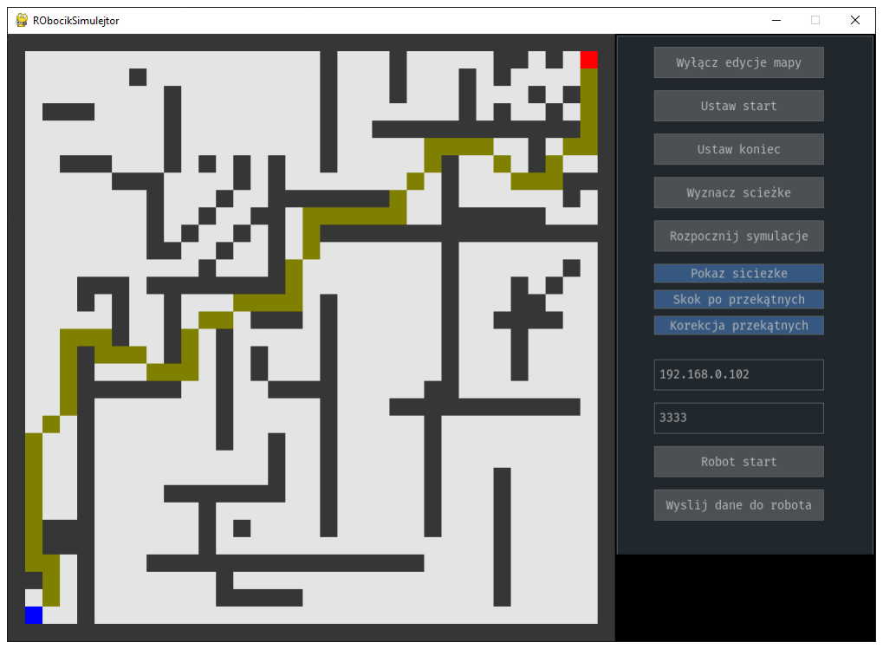
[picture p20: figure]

Rysunek 6.17: Wyznaczona ścieżka, włączona korekcja i przejście po przekątnej

Jak widać na powyższym zdjęciu punkt docelowy został osiągnięty i robot przejechał po

wyznaczonej ścieżce. Dzięki wymienionym wcześniej opcjom robot tam gdzie to jest możliwe

przejeżdża po skosie i zmniejsza czas przejazdu.

W kolejnym teście została wyłączona korekcja przekątnych.

Rysunek 6.18: Wyznaczona ścieżka, korekcja przekątnych jest wyłączona

Jak widać ścieżka znacząco zmieniła się w porównaniu do poprzedniego rozwiązania.

Teoretycznie została wyznaczona najkrótsza ścieżka, jednak w praktyce robot nie byłby w

stanie jej przejechać. W niektórych przypadkach skoku widać że robot nie miałby miejsca na

przejazd.

W poniższym przypadku ścieżka trasowana bez przejścia po przekątnych.

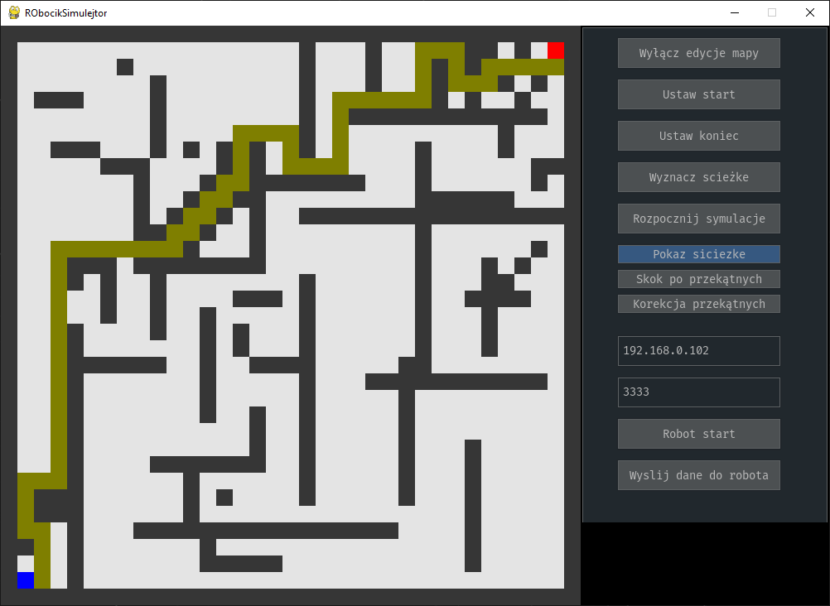
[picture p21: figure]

Rysunek 6.19: Najkrótsza trasa, wyłączone przejście po przekątnych

Porównując wynik do obu poprzednich przypadków widzimy że algorytm znacznie zmie-

nił trasę po, której przejeżdża robot i przechodzi do następnego sąsiada tylko na wprost a więc

w tym przypadku będzie najwięcej skoków.

### 6.2. Sprawdzenie wpływu funkcji heurestycznej na ścieżkę

Poniższy test będzie miał za zadanie sprawdzić wpływ wybranej funkcji heurestycznej

na wygenerowaną ścieżkę.

### 6.2.1. Funkcja Eukalidesowa

W pierwszej kolejności zostanie sprawdzona domyślna wybrana funkcja heurestyczna

opisana wzorem (3.2). Rezultat działania algorytmu widoczny jest poniżej.

Jednokrotne wzmocnienie

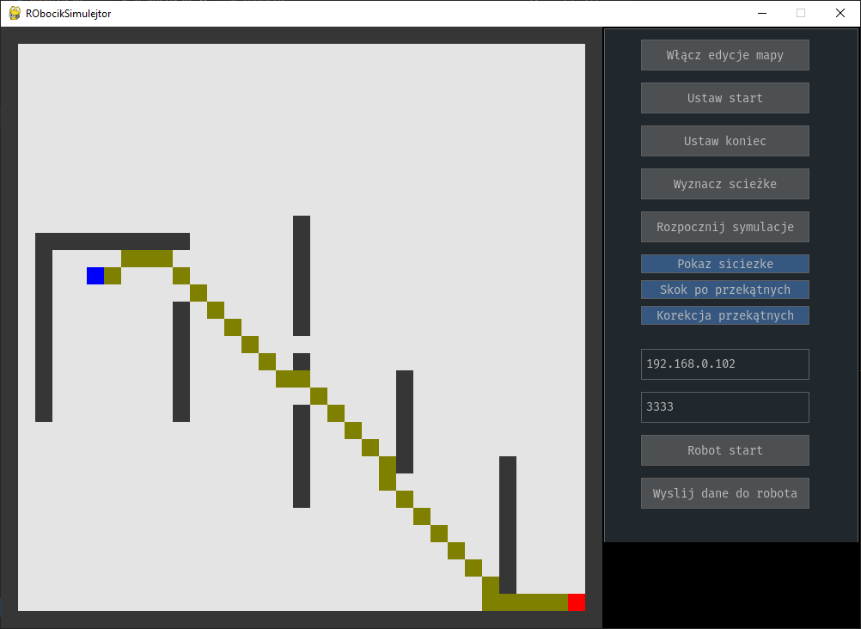
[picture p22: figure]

Rysunek 6.20: Wyznaczona ścieżka, funkcja Eukalidesowa k=1

Dziesięciokrotne wzmocnienie

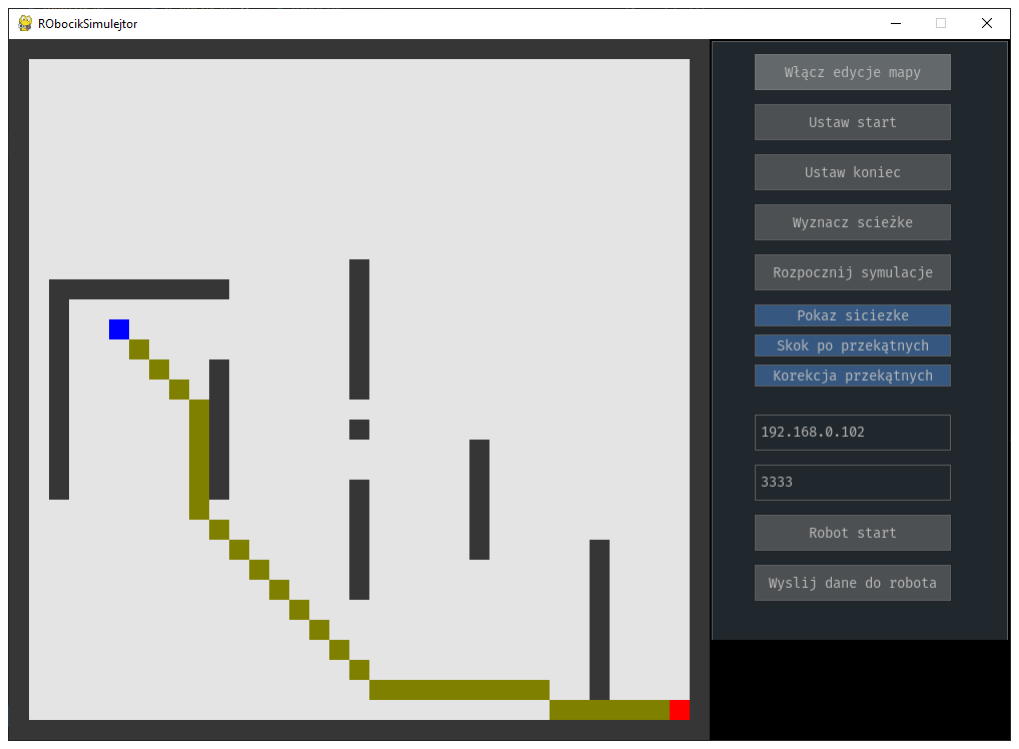
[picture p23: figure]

Rysunek 6.21: Wyznaczona ścieżka, funkcja Eukalidesowa k=10

Wzmocnienie k=1.41

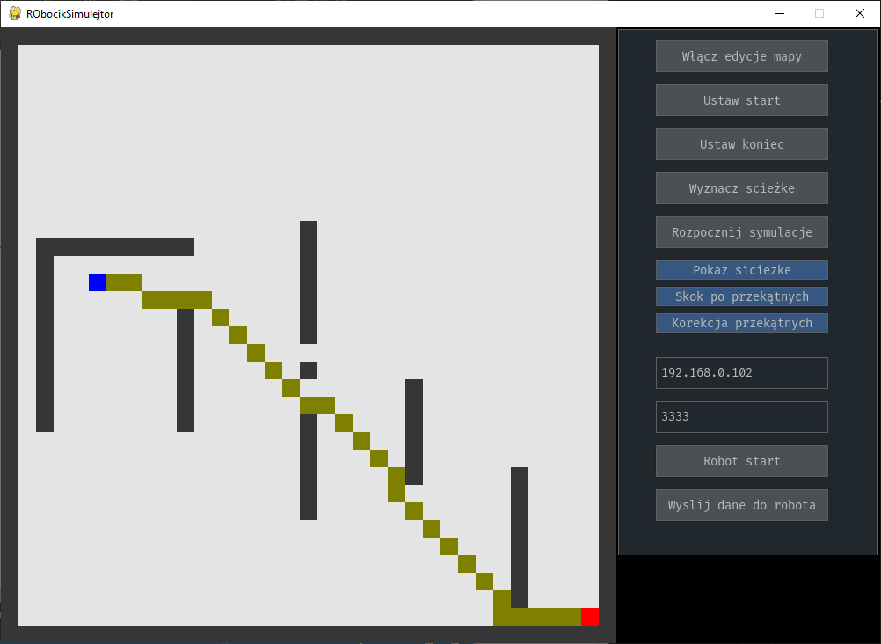
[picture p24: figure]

Rysunek 6.22: Wyznaczona ścieżka, funkcja Eukalidesowa k=1.41

### 6.2.2. Metryka miejska

Kolejny test przeprowadzi wpływ metryki miejskiej opisanej wzorem nr. (3.3)


Rysunek 6.23: Wyznaczona ścieżka, metryka miejska

### 6.2.3. Dystans oktalny

Ostatnie sprawdzona heurestyka implementuje dystans oktalny opisany wzorem nr. (3.4)


Rysunek 6.24: Wyznaczona ścieżka, dystans oktalny

Jak widać na powyższych zrzutach ekranu funkcje heurestyczne mają bardzo duży wpływ

na wygenerowaną trasę i jej wybór może być uzależniony od środowiska, w którym porusza się

robot. W tym przypadku funkcja Eukalidesowa ze wzmocnieniem 1.41 jest optymalna, generuję

najkrótszą ścieżkę z długimi prostymi odcinkami co w przypadku realnego robota przyśpieszy

przejazd.

### 6.3. Test komunikacji z fizycznym robotem

Poniższy test ma na celu sprawdzenie komunikacji pomiędzy zbudowanym robotem a

programem do sterowania. Aby przeprowadzić test, został napisany prosty graficzny program

pozwalający na ręczne sterowanie robotem. Po za nim istnieje konsola z możliwością wprowa-

dzania i wysyłania komend. W pierwszej kolejności należy poznać adres sieciowy jaki robot

dostał od serwera DHCP. Aby to zrobić należy podłączyć mikrkontroler do komputera poprzez

kabel usb i zainstalowaną przejściówkę USB-UART. Po uruchomieniu monitora odczytującego

dane ze wskazanego portu, można odczytać adres.

Rysunek 6.25: Odczytany adres IP

W następnym kroku możemy połączyć się przy pomocy konsoli lub dedykowanego pro-

gramu.

Rysunek 6.26: Testowe połączenie z konsoli


Rysunek 6.27: Testowe połączenie do sterowania ręcznego

Po połączeniu z robotem możliwe jest ręczne sterowanie przy pomocy dedykowanych

przycisków lub klawisze w,s,a i d. Jeżeli wprowadzony adres ip jest błędny, w konsoli pojawi

się odpowiedni komunikat opisujący błąd.

## 7. Podsumowanie projektu

Implementacja algorytmu i symulatora

Analizując wyniki otrzymane podczas testowania algorytmu możemy zauważyć że wy-

znaczona ścieżkę jest optymalna. Podczas testów sprawdzono wpływ różnych funkcji heure-

stycznych na otrzymaną ścieżkę. Na ich podstawie widać że takie funkcje mają duże znacze-

nie i w zależności od skomplikowania otoczenia, odległości oraz dostępnych ruchów(możliwość

przejścia po przekątnej) otrzymujemy ścieżki o różnym poziomie skomplikowania. Zaimplemen-

towanie algorytmu w pythonie pozwoliło na szybkie i sprawne jego przetestowanie, jednak w

przypadku dużych i skomplikowanych map można było odczuć coraz dłuższe przeliczanie. W

znacznej mierze wynika to ze ścisłego połączenia algorytmu z symulatorem i co za tym idzie

wymuszone ciągłe przeszukiwanie tablicy z przeszkodami. Można to naprawić poprzez wy-

generowanie grafu z tylko najpotrzebniejszymi informacjami przed uruchomieniem algorytmu,

dzięki czemu zredukuje się liczba niepotrzebnych wywołań funkcji.

Równocześnie została potwierdzona teza z literatury, mówiąca o prostocie algorytmu a co

za tym idzie możliwości stosowania go w różnych zastosowaniach między innymi do wyznaczania

ścieżki w sieciach komputerowych.

Budowa robota

Zbudowany robot był zbyt lekki na przodzie przez co w niektórych przypadkach (szcze-

gólnie podczas ruszania) podnosił się. Komunikacja bazująca na wifi i serwerze tcp sprawdzała

się dobrze i robot odbierał polecenia bez zauważalnych opóźnień. Dzięki systemowi poleceń

tekstowych możliwe jest proste rozbudowanie oprogramowania pozwalające na odbieranie i pre-

zentowanie danych takich jak prędkość kół napędowych. Ostatecznie nie udało się przetestować

działania algorytmu na robocie, ponieważ uszkodzeniu uległ główny sterownik. Prawdopodob-

nie uszkodzenie wynika z zastosowania nieoryginalnego sterownika do silników i pojawienia się

na liniach sygnałowych napięcia większego niż 3,3V.

Należy pamiętać że w prawdziwym autonomicznym robocie (na przykład przewożącym

towar w magazynie) sam algorytm wyznaczający trasę nie będzie wystarczający. Algorytm

bazuje na mapie otoczenia a w praktyce ta będzie się bardzo często zmieniać więc najlepiej

aby ten sam skanował otoczenie i dynamicznie dobierał optymalne rozwiązanie. Finalnie duży

wpływ na czas przejazdu będzie miała heurestyka, krótsza trasa z dużą ilością skrętów może

mieć większy czas przejazdu niż potencjalnie dłuższa, na której robot może osiągnąć prędkość

maksymalną.

## Literatura

[1] Path Planning with Modified a Star Algorithm for a Mobile Robot DOI:

10.1016/j.proeng.2014.12.098

[2] https://openslam-org.github.io/ Dostęp 16.01.2023
[3] https://wiki.ros.org/hector_slam Dostęp 16.01.2023
[4] https://people.eecs.berkeley.edu/ klein/papers/pcfg-astar.pdf doi:10.3115/1073445.1073461
[5] Cui, Xiao & Shi, Hao. (2010). A*-based Pathfinding in Modern Computer Games. 11.
[6] Ghassan Fadlallah, Hamid Mcheick, Djamal Rebaine (2020) Internet-of-Things (IoT) Shor-

test Path Algorithms and Communication Case Studies for Maintaining Connectivity in

Harsh Environements

[7] https://docs.espressif.com/projects/esp-idf/en/latest/esp32/get-started/index.html. Do-

stęp 04.01.2023.

[8] https://medium.com/dish/75-years-of-innovation-shakey-the-robot-385af2311ec8 Dostęp

04.01.2023.

[9] https://www.pygame.org/docs/ Dostęp 06.01.2023
[10] https://pygame-gui.readthedocs.io/en/latest/ Dostęp 06.01.2023
[11] https://think-async.com/Asio/ Dostęp 06.01.2023
[12] https://www.cs.cmu.edu/ motionplanning/lecture/lec20.pdf Dostęp 10.01.2023
[13] https://www.mathworks.com/discovery/slam.html Dostęp 10.01.2023

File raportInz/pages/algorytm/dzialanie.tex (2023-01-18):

\subsection{Opis działania algorytmu}

A* to heurestyczny algorytm wyznaczający najkrótszą możliwą ścieżkę w grafie. 
Jest to algorytm zupełny i optymalny, a więc zawsze zostanie wyznaczone optymalne 
rozwiązanie. Ze względu na przeszukiwanie oparte na grafie algorytm działa najlepiej na strukturze drzewiastej.
Zadaniem algorytmu jest minimalizacja funkcji:
\begin{equation}
	f(x)=h(x) + g(x)
	\label{Eq:funkcjaKosztuAStar}
\end{equation}
gdzie: $f(x)$ - minimalizowana funkcja, $g(x)$ - to rzeczywisty koszt dojścia do punktu x.

Funkcja $h(x)$ to funkcja heurestyczna, oszacowuje ona koszt dotarcia od punktu x do wierzchołka docelowego

Zalety:
\begin{itemize}
	\item jest kompletny i optymalny
	\item może przeszukiwać skomplikowane mapy
	\item jest najwydajniejszym takim algorytmem
\end{itemize}
Wady:
\begin{itemize}
	\item jego wydajność w znacznej mierze zależy od funkcji heurestycznej
	\item Każda akcja ma stały koszt wykonania
	\item nie nadaje się do często zmieniającego się otoczenia robota, wymaga ponownego przeliczenia
\end{itemize}

\textbf{Przykładowe funkcje heurestyczne:}
\begin{itemize}
	\item Funkcja euklidesowa
	      \begin{equation}
	      	h(x) = K * \sqrt[2]{(x_1 - x_2)^2 + (y_1 - y_2)^2}
	      	\label{Eq:heuresticEucalides}
	      \end{equation}
	\item Geometria Manhattanu (inaczej metryka miejska)
	      \begin{equation}
	      	h(x) = |x_2 - x_1| + |y_2 - y_1|
	      	\label{Eq:heuresticManhattanu}
	      \end{equation}
	\item Odległość oktylowa
		\begin{equation}
			h(x) = D1 * (|x_1 - x_2| + |y_1 - y_2|) + (D2 - 2*D1) * min(|x_1 - x_2|, |y_1 - y_2|)
			\label{Eq:heuresticOctileDistance}
		\end{equation}

\end{itemize}
Gdzie: $x_1$ i $y_1$ to współrzędne wyznaczanego punktu, $x_2$ i $y_2$ to koordynaty celu, $K$ - oznacza wzmocnienie, $D1$ - koszt skoku na wprost, $D2$ - koszt skoku po przekątnej

\subsection{Analiza innych algorytmów}
\begin{itemize}
	\item{ \textbf{RRT(Rapidly-exploring random tree)}\cite{RRTLec} - to algorytm generujący i łączący 
	losowe punkty w przestrzeni. Z każdym wygenerowanym wierzchołkiem sprawdzane jest czy ten omija przeszkody.
	a jego działanie kończy się gdy wygenerowany węzeł jest we wskazanym regionie lub zostanie osiągnięty limit.
	Jego zalety to:
		\begin{itemize}
			\item Balans pomiędzy zachłannością a eksploracją
			\item prosty i szybki w implementacji
			\item Zbiega się z rozkładem próbkowania
		\end{itemize}
	wady:
		\begin{itemize}
			\item jest czuły na metrykę
			\item duża złożoność obliczeniowa
		\end{itemize}
	}
	\item{\textbf{SLAM(Simultaneous localization and mapping)} \cite{SLAMMat} - jest metodą używaną w autonomicznych 
	pojazdach. Pozwana na zbudowanie oraz lokalizacje pojazdu względem otoczenia na mapie. Algorytm ten nie wyznacza bezpośrednio
	ścieżki omijającej przeszkody jednak w praktyce jest ważnym elementem takiego systemu. Każdy ruch robota w rzeczywistym 
	środowisku jak i sama mapa obarczona jest pewnym błędem powodującym że robot znajduje się w innym miejscu niż zakładamy. 
	Możemy wyróżnić działanie algorytmu w oparciu o lidary albo o metody wizyjne. Wadą metody jest wysoki koszt obliczeniowy 
	i narastający z czasem błąd pozycji co w konsekwencji może spowodować utratę pozycji.
	\begin{figure}[H]
		\centering
		
		\caption{Przykład mapowania metodą SLAM\cite{SLAMMat}}
	\end{figure}
	}
\end{itemize}

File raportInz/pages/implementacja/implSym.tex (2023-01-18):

Środowisko symulacyjne zostało napisane w języku Python i bibliotekach pygame\cite{dokPygame} i pygame\_gui\cite{dokPygameGui},
zapewniających obsługę graficznego interfejsu użytkownika. 
\begin{lstlisting}[language=Python,caption=Uruchomienie aplikacji,label={kodPythonStartApki}]
if __name__ == '__main__':
    app = App()
    app.main()
\end{lstlisting}

\textbf{Obsługa mapy}

Dla logicznego podzielenia programu została napisana główna klasa programu o nazwie App.
Takie podejście pozwoliło na odseparowanie poszczególnych funkcji aplikacji. 
W pierwszej kolejności konstruktor obiektu aplikacji, generuje okno, tworzy 
graficzne elementy użytkownika oraz ustawia odpowiednie flagi informujące o stanie aplikacji. 
Dalej wywoływana jest funkcja main wczytująca odpowiednią mapę z pliku, a następnie uruchamiająca 
główną pętlę programu działającą w 60 klatkach na sekundę.

\begin{figure}[H]
	\centering
	
	\caption{Schemat głównej pętli programu}
	\label{fig:schematPetliGlownej}
\end{figure}

Aby uprościć symulowanie różnych scenariuszy i rozmiarów map otoczenia, ta ładowana jest ze wskazanego w 
programie pliku. Wskazany plik jest w formacie json i podzielony jest na dwie sekcje. 
Pierwsza dostarcza informacji o samej mapie, natomiast druga o poruszającym się po niej robocie. 
Sekcja mapy zawiera lokalizacje do pliku tekstowego z zapisanymi elementami. 

\begin{lstlisting}[language=Python,caption=Uruchomienie aplikacji,label={kodPythonWczytanieMapy}]
(self.map, self.robot) = MapLoader.fromJson("maps/m02.json")
\end{lstlisting}
Ładowaniem wszystkich tych informacji zajmuje się specjalna metoda w klasie MapLoader, wywołana przed uruchomieniem pętli głównej programu.
Wczytywana mapa jest w postaci siatki i każdy jej element ma stały rozmiar. Symulator rozróżnia kilka typów węzłów:
\begin{itemize}
	\item brak elementu - możliwy przejazd 
	\item ściana - przeszkoda do ominięcia przez algorytm
	\item punkt początkowy - od niego rozpoczyna się wyznaczanie ścieżki, jest zdefiniowany przez użytkownika
	\item punkt końcowy - analogicznie jak w poprzednim przypadku
	\item ścieżka - element wyznaczonej trasy
\end{itemize}

Wszystkie wymienione typy zapisane są w klasie Tile, reprezentującej pojedynczy rysowany i zapisywany w pliku kwadrat.
Użytkownik może w każdej chwili działania aplikacji edytować mapę a  przed zamknięciem programu 
zaktualizowana mapa jest zapisywana do pliku. Wyjątkiem jest obiekt będący elementem ścieżki, 
ten nie jest zapisywany do pliku, ponieważ generowany jest dynamicznie i służy tylko do reprezentacji wygenerowanej ścieżki.

\textbf{Wyznaczanie ścieżki i symulacja}

Po załadowaniu program oczekuje na akcje użytkownika i ewentualne uruchomienie wyznaczania ścieżki lub całej symulacji.
\begin{lstlisting}[language=Python,caption=Uruchomienie aplikacji,label={kodPythonWyznaczenieSciezki}]
elif ev.ui_element == self._startAStar:
    star = AStar(self.map.map, self.map.getSize())
    star.diagonalJump(self._diagonalJump)
    star.diagolnalCorrection(self._diagonalCorrextion)
    self.path       = star.findPath2(Node(self.map.getStartCords()), Node((self.map.getEndCords())))
    self._pathExist = True
    self.robot.stopSimulation()
    self.robot.hideRobot()
\end{lstlisting}

Po kliknięciu w przycisk odpowiadający za wyznaczenie i pokazanie ścieżki, program tworzy obiekt 
wyznaczający trasę i ustawia dodatkowe opcje algorytmu (np. skok po przekątnych). 
Dalej pobierana jest wyznaczona trasa będąca tablicą kolejnych punktów, po których należy przejść aby dojść do celu.
Na końcu ustawiana jest odpowiednia flaga programu, zatrzymywana jest symulacja i ukrywany jest robot (mamy nowo wyznaczoną trasę).
Przycisk uruchamiający symulacje sprawdza czy istnieje ścieżka i w razie potrzeby ją generuje. Następnie trasa podawana 
jest do obiektu robota odpowiadającego za symulacje i dalej jest ona uruchamiana.

\textbf{Przejście robota po ścieżce}

Symulator robota pobiera pierwszy punkt, do którego ma dotrzeć. Zmiana pozycji odbywa się poprzez regulator typu P z 
ustawioną nastawą na wskazany punkt. Wartość wzmocnienia proporcjonalnego wczytana jest z pliku i oznaczona jest jako szybkość robota.
Dalszy etap to sprawdzenie czy symulowany robot dotarł do celu. 
\begin{lstlisting}[language=Python,caption=Uruchomienie aplikacji,label={kodPythonSprawdzenieCeluRobota}]
if abs(deltaPos0) < 0.2 and abs(deltaPos1) < 0.2:
            self._currentTarget -= 1
\end{lstlisting}
Realizowane jest to poprzez sprawdzenie czy wartość bezwzględna z różnicy aktualnej oraz docelowej pozycji jest mniejsza niż 0,1.
Po osiągnięciu punktu, ustawiany jest nowy indeks tablicy wskazujący na kolejny cel.
Jeżeli na początku aktualizacji indeks jest ujemny to robot przejechał po całej wyznaczonej trasie.

\textbf{Komunikacja z robotem}
% polaczenie z robotem po tcp

Po wyznaczeniu ścieżki symulator na polecenie użytkownika może połączyć się ze zbudowanym robotem aby ten osiągnął założony cel.
Zgodnie ze schematem \ref{sch:ogolnyRozwiazania} robot po połączeniu z siecią WiFi i utworzeniu serwera TCP oczekuje na wysyłane komendy.
Aplikacja podczas uruchamiania, tworzy gniazdo, które potem zostanie wykorzystane do połączenia. 
\begin{lstlisting}[language=Python,caption=Utworzone gniazdo,label={kodPythonGniazdo}]
self._robotSocket       = socket.socket(socket.AF_INET, socket.SOCK_STREAM)
\end{lstlisting}
Dla zwiększenia elastyczności utworzone zostały dwa pola tekstowe pozwalające na wprowadzenie adresu ip oraz portu z uruchomionym serwerem.
Po wprowadzeniu wymaganych danych operator może spróbować nawiązać połączenie z robotem poprzez specjalny przycisk.

\begin{lstlisting}[language=Python,caption=Nawiązanie połączenia,label={kodPythonGniazdo}]
if self._robotSocketFlag is True:
    self._robotSocket.close()

print(f"Laczenie z robotem {(self._textRobotIp.get_text(), int(self._textRobotPort.get_text()))}")
self._robotSocket.settimeout(1)
try:
    self._robotSocket.connect((self._textRobotIp.get_text(), int(self._textRobotPort.get_text())))
    self._robotSocketFlag = True
    self._sendCommandToRobot("setMode auto")
    print("Podlaczono!!!")
except Exception as err:
    self._robotSocketFlag = False
    print(f"Blad polaczenia z robotem")
    print(err)
\end{lstlisting}
W pierwszej kolejności sprawdzana jest flaga informująca o stanie połączenia, jeżeli jest aktywne to jest ono zamykane.
Na utworzonym gnieździe wywoływana jest funkcja connect z wprowadzonymi przez użytkownika parametrami.
Cała operacja zamknięta jest w bloku try..except a więc jeżeli program nie połączy się z robotem to wyświetlana jest odpowiednia informacja. 
Podczas łączenia należy zwracać uwagę na podsieci, w których jest robot i sterujący laptop. 
Dodatkowo robot posiada dynamiczne ip co zostało szerzej opisane w rozdziale o oprogramowaniu robota.
Jeżeli żaden wyjątek nie został rzucony to wysyłana jest pierwsza komenda ustawiająca tryb robota na automatyczny.

\begin{lstlisting}[language=Python,caption=Wysyłanie komendy do robota,label={kodPythonSendCmd}]
def _sendCommandToRobot(self, cmd):
    if self._robotSocketFlag is False:
        print("Robot nie podlaczony!!")
        return
    
    try:
        self._robotSocket.send(str.encode(cmd))
    except OSError as err:
        print("Robot nie podlaczony!!!")
        self._robotSocket.close()
        self._robotSocketFlag = False
        return
\end{lstlisting}
Program może wysłać dowolną komendę poprzez metodę sendCommandToRobot. 
Podobnie jak przy połączeniu, metoda wysyłająca dane może rzucić wyjątek o braku połączenia. W takim przypadku
wyświetlana jest odpowiednia informacja i resetowana jest flaga połączenia. 

\textbf{Finalna wersja programu}

Na poniższym zrzucie widać uruchomiony program z trwającą symulacją. Po prawej stronie został umieszczony panel 
z interfejsem użytkownika. Po lewej stronie widoczna jest wczytana mapa. 
Kolorem niebieskim został oznaczony punkt startowy a czerwonym końcowy.
Żółte kratki oznaczają wyznaczoną przez algorytm ścieżkę, po której przejdzie robot. Szare pola to przeszkody, które robot ma ominąć. 
Robot oznaczony jest przez jasno-zielone koło, które przesuwa się po mapie. 

\begin{figure}[H]
	\centering
	
	\caption{Widok finalnej wersji programu}
	\label{fig:finalnaWersjaProgramu}
\end{figure}

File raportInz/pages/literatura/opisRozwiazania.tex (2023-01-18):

\subsection{Opis przyjętego rozwiązania}
Algorytm wyznaczania najkrótszej ścieżki wraz z środowiskiem testowym został napisany w języku Python.
Implementacja algorytmu nie wymaga żadnych dodatkowych bibliotek. Do zbudowania środowiska symulacyjnego 
zostały użyte biblioteki graficzne do rysowania kształtów geometrycznych oraz podstawowych elementów graficznego 
interfejsu użytkownika. 
Weryfikacja działania algorytmu  została przeprowadzona na zbudowanym trójkołowym robocie.
Oprogramowanie robota zostało napisane w języku C++ i dodatkowych bibliotekach udostępnionych przez producentów użytych sterowników.

\begin{figure}[H]
	\centering
	
	\caption{Ogólny schemat projektu}
	\label{sch:ogolnyRozwiazania}
\end{figure}

Użytkownik po uruchomieniu środowiska symulacyjnego będzie miał możliwość edycji mapy opartej na siatce, określenia punktu początkowego i końcowego.
Kolejnym krokiem jest wyznaczenie ścieżki oraz jej graficznej reprezentacji. Tak wyznaczoną ścieżkę można wysłać do robota 
operującego w środowisku rzeczywistym.

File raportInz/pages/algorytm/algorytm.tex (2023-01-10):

\section{Algorytm A*}
\subsection{Geneza powstania}
Algorytm A* powstał w ramach projektu Shakey, zapoczątkowanego w 1966 roku przez Charles Rosen'a.
Celem projektu było zbudowanie robota, który potrafiłby planować własne działania. 
Zbudowany robot wyróżniał się na tle innych tym że integrował kilka różnych modeli sztucznej 
inteligencji pracującej jako jeden system.

Robot został zbudowany z:
\begin{itemize}
	\item kamery telewizyjnej i dalmierza optycznego - system wizyjny do obserwacji środowiska
	\item łącza radiowego - służącego do komunikacji z bazą, odbierania i wysyłania komend
	\item detektora uderzeń - pozwalający na zatrzymanie robota w przypadku kolizji
\end{itemize}

Komunikacja odbywała się poprzez wysyłane radiowo, tekstowe polecenia mające określoną strukturę np.:
GOTO D4 - co oznaczało automatyczne przemieszczenie się robota do wskazanej pozycji
\begin{figure}[H]
	\centering
	
	\caption{Robot Shakey i Charles Rosen, inicjator projektu \cite{robotShakey}}
	\label{fig:Rys}
\end{figure}

\input{pages/algorytm/dzialanie}

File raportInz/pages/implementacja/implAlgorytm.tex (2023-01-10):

Mechanizm wyszukiwania najkrótszej ścieżki został zamknięty w jednym module o nazwie aStar.
Na moduł składa się klasa AStar ze wszystkimi potrzebnymi metodami oraz dodatkowa klasa Node reprezentująca 
pojedynczy punkt przeszukiwanego grafu.

Wyznaczanie najkrótszej ścieżki rozpoczyna się od wyznaczenia kosztu punktu startowego i utworzenia zbioru z nieprzeszukanymi 
wierzchołkami, do którego dopisujemy punkt początkowy. 
\begin{lstlisting}[language=Python,caption=Przygotowanie danych,label={kodPython}]
    openList = []
    startNode.h = self.heurestic(startNode.getCords(), endNode.getCords())
    startNode.g = 0
    heappush(openList, startNode)
\end{lstlisting}

Wewnętrzna funkcja heurestic przyjmująca pozycje dwóch punktów odpowiada
za wyliczenie optymistycznego kosztu przejścia od punktu x do wierzchołka docelowego.
Takie podejście pozwala na szybką podmianę funkcji bez znaczących zmian w programie.
Wykorzystywana funkcja heurestyczna to równanie nr. \eqref{Eq:heuresticEucalides} 

W kolejnym kroku uruchamiana jest pętla, która wykonywana jest dopóki
w zbiorze otwartym znajdują się nie odwiedzone elementy. Z listy pobierany jest 
element o najmniejszej liczbie punktów co oznacza, że dany wierzchołek drzewa ma największe szanse być najlepszym rozwiązaniem.
Jeżeli pobrany element nie jest celem to dalej pobierani i przetwarzani są wszyscy jego sąsiedzi. 
W tym rozwiązaniu, dla zaoszczędzenia pamięci, symulator przechowuję tylko przeszkody.
W związku z tym do pobrania sąsiadów używana jest specjalna funkcja sprawdzająca czy na mapie o wskazanych koordynatach istnieje punkt. 
Jeżeli takowy obiekt nie istnieje to oznacza, że algorytm może użyć tych współrzędnych do trasowania ścieżki. 
Od tej części programu zależy, czy algorytm ma wyznaczyć ścieżkę uwzględniając skoki po skosie.

\begin{lstlisting}[language=Python,caption=Wyznaczenie kosztu ścieżki,label={kodPython2}]
neighborNode = self._findNodeOnList(openList, newCords)
if neighborNode is None:
    neighborNode = Node(newCords)
    neighborNode.g = COST
    neighborNode.h = self.heurestic(newCords, endNode.getCords())
    neighborNode.parent = currentNode
    openList.append(neighborNode)

distance_from_curr_to_neighbor = COST
scoreFromStartToCurrentNeighbor =  currentNode.g + distance_from_curr_to_neighbor

if neighborNode.getScore() <= currentNode.getScore():
    neighborNode.g = scoreFromStartToCurrentNeighbor
    neighborNode.h = scoreFromStartToCurrentNeighbor + self.heurestic(newCords, endNode.getCords())     
    neighborNode.parent = currentNode
\end{lstlisting}

Powyższy kod odpowiada za wyznaczenie kosztu przejścia do sąsiada. Jeżeli punkt nie istnieje jeszcze w otwartym zbiorze 
to jest tworzony i do niego dodawany. Zgodnie z założeniem całkowity koszt to suma rzeczywistego kosztu dystansu i wyniku funkcji heurestycznej. 
Rzeczywisty koszt (funkcja $g(x)$) jest ustalony na sztywno i zależy od współrzędnych, do których skaczemy. 
Jeżeli następny punkt jest na wprost to koszt wynosi 10.
Jako iż przechodzimy po siatce z węzłami o stałej i równej odległości to koszt skoku do sąsiada po skosie został wyznaczony z twierdzenia Pitagorasa. 
Należy zwrócić uwagę, że jeżeli całkowity koszt jest mniejszy od aktualnego to węzeł ma ustawianego rodzica, ma to duże znaczenie w przypadku wyjścia z pętli 
i wyznaczenia najkrótszej trasy spośród wszystkich kosztów. 

\begin{lstlisting}[language=Python,caption=Przygotowanie danych,label={kodPython3}]
if currentNode == endNode:
    path = []
    while currentNode is not None:
        path.append(currentNode)
        currentNode = currentNode.getParent()
    return path
else:
    return []
\end{lstlisting}

Po zakończeniu pętli, sprawdzane jest czy została znaleziona ścieżka, jeżeli takowa istnieje to w kolejnej pętli 
wyznaczane są przy pomocy pola wskazującego na rodzica kolejne punkty trasy. 
Jeżeli węzeł nie jest punktem końcowym to trasa nie została znaleziona i zwracana jest pusta lista.

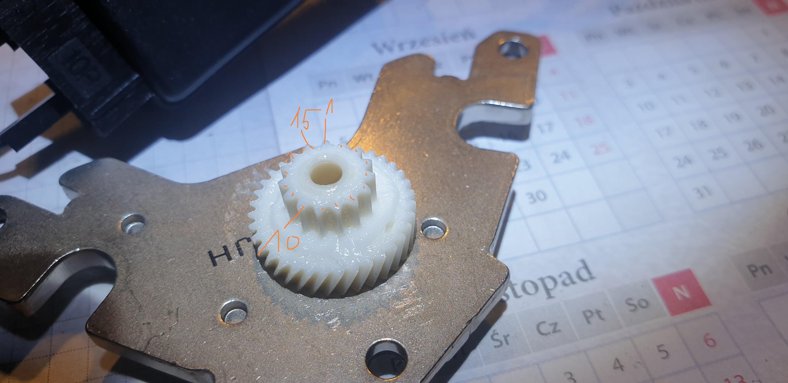
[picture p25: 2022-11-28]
robot/cady/przekladniaSilnika/z2_2.jpg

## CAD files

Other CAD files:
robot/cady/robotCad.f3z

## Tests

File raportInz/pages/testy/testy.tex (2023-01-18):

\section{Przeprowadzone testy}

Do testów zostanie wykorzystana mapa o rozmiarze 35x35 bloków.

\subsection{Wpływ ustawień na wyznaczoną ścieżkę}

W pierwszym eksperymencie został włączony skok po
przekątnej i korekcja wynikająca z tego błędów.

\begin{figure}[H]
	\centering
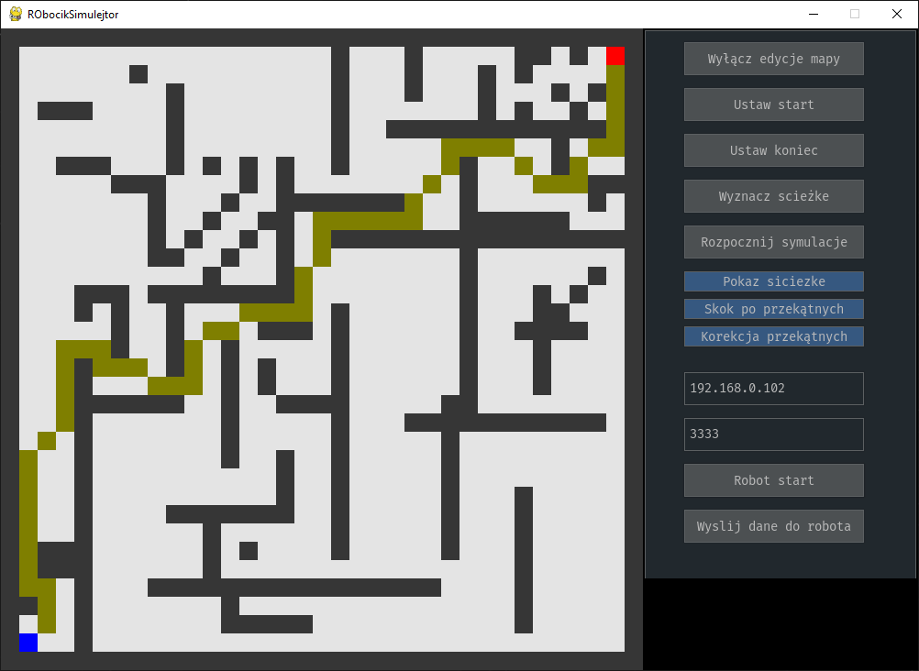
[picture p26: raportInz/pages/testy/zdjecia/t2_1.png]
	
	\caption{Wyznaczona ścieżka, włączona korekcja i przejście po przekątnej}
\end{figure}

Jak widać na powyższym zdjęciu punkt docelowy został osiągnięty i robot przejechał po wyznaczonej ścieżce.
Dzięki wymienionym wcześniej opcjom robot tam gdzie to jest możliwe przejeżdża po skosie i zmniejsza czas przejazdu. 

W kolejnym teście została wyłączona korekcja przekątnych.
\begin{figure}[H]
	\centering
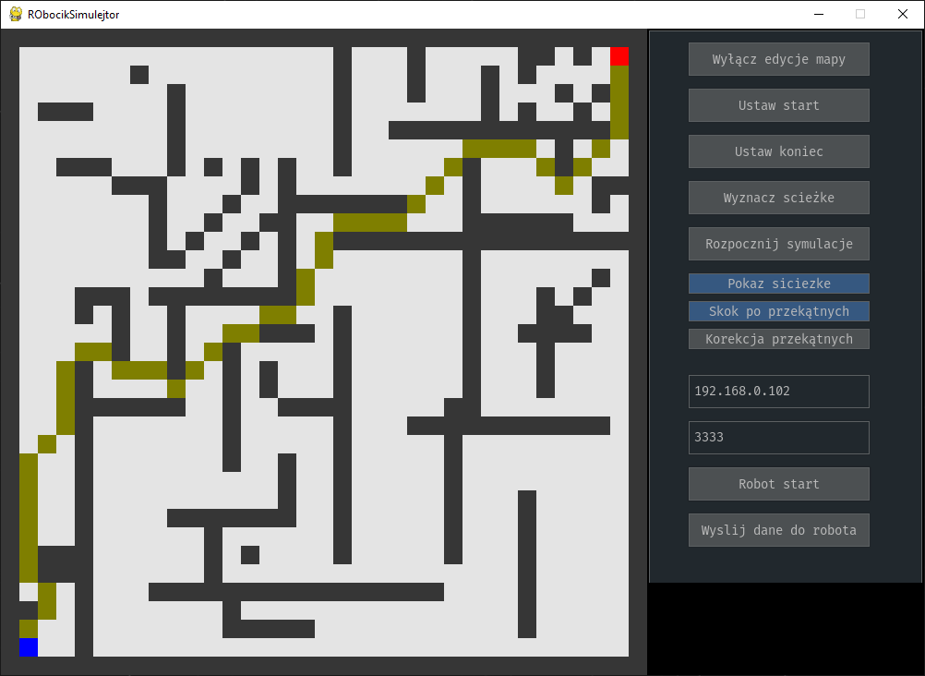
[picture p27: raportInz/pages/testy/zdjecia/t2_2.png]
	
	\caption{Wyznaczona ścieżka, korekcja przekątnych jest wyłączona}
\end{figure}

Jak widać ścieżka znacząco zmieniła się w porównaniu do poprzedniego rozwiązania. Teoretycznie została wyznaczona najkrótsza 
ścieżka, jednak w praktyce robot nie byłby w stanie jej przejechać. 
W niektórych przypadkach skoku widać że robot nie miałby miejsca na przejazd.

W poniższym przypadku ścieżka trasowana bez przejścia po przekątnych. 

\begin{figure}[H]
	\centering
	
	\caption{Najkrótsza trasa, wyłączone przejście po przekątnych}
\end{figure}
Porównując wynik do obu poprzednich przypadków widzimy że algorytm znacznie zmienił trasę po, której przejeżdża robot
i przechodzi do następnego sąsiada tylko na wprost a więc w tym przypadku będzie najwięcej skoków.

\clearpage
\subsection{Sprawdzenie wpływu funkcji heurestycznej na ścieżkę}
Poniższy test będzie miał za zadanie sprawdzić wpływ wybranej funkcji heurestycznej na wygenerowaną ścieżkę.
\subsubsection{Funkcja Eukalidesowa}
W pierwszej kolejności zostanie sprawdzona domyślna wybrana funkcja heurestyczna opisana wzorem \eqref{Eq:heuresticEucalides}.
Rezultat działania algorytmu widoczny jest poniżej.

\textbf{Jednokrotne wzmocnienie}
\begin{figure}[H]
	\centering
	
	\caption{Wyznaczona ścieżka, funkcja Eukalidesowa k=1}
\end{figure}
\textbf{Dziesięciokrotne wzmocnienie}

\begin{figure}[H]
	\centering
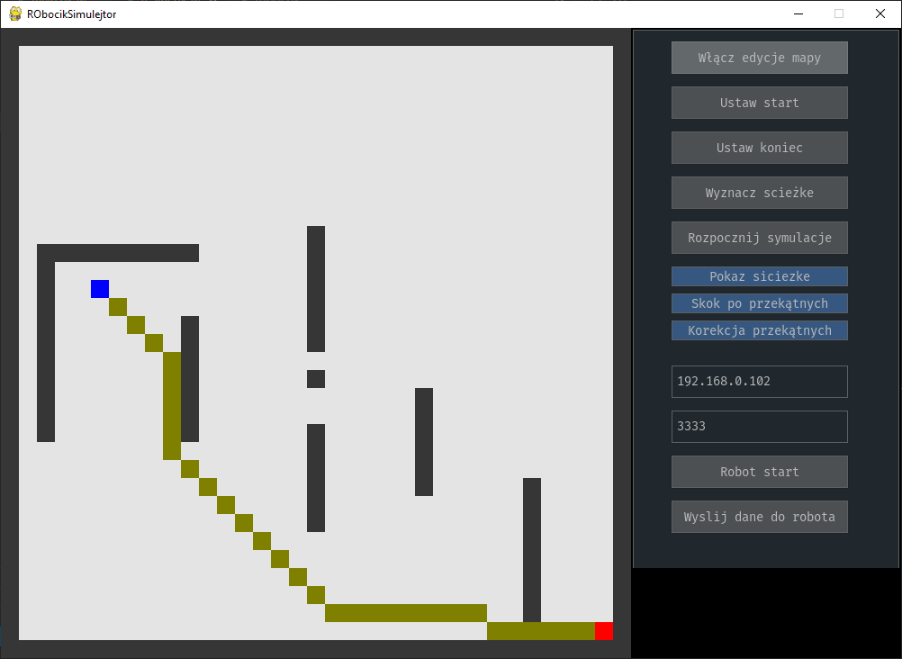
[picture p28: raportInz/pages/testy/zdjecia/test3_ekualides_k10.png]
	
	\caption{Wyznaczona ścieżka, funkcja Eukalidesowa k=10}
\end{figure}
\textbf{Wzmocnienie k=1.41}

\begin{figure}[H]
	\centering
	
	\caption{Wyznaczona ścieżka, funkcja Eukalidesowa k=1.41}
\end{figure}

\subsubsection{Metryka miejska}
Kolejny test przeprowadzi wpływ metryki miejskiej opisanej wzorem nr. \eqref{Eq:heuresticManhattanu}

\begin{figure}[H]
	\centering
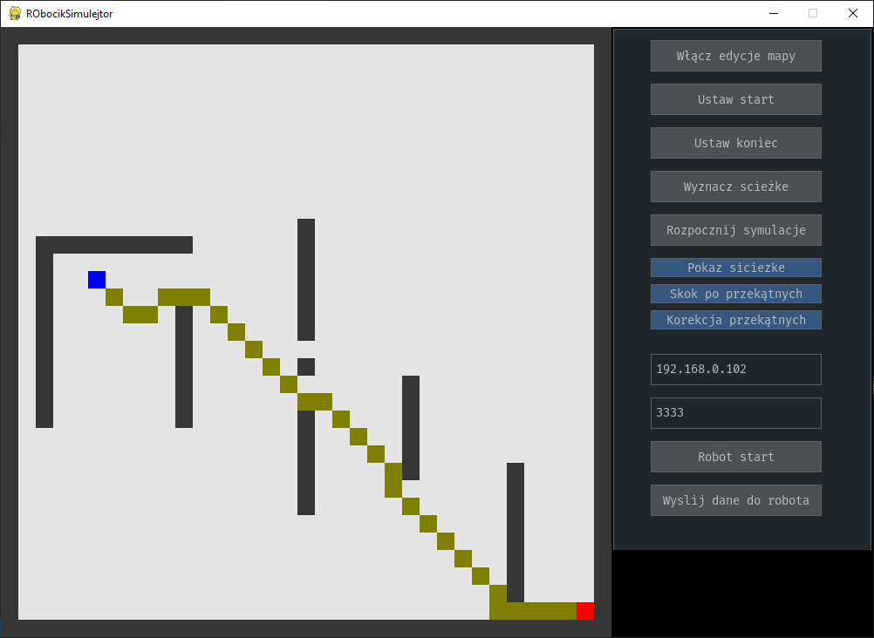
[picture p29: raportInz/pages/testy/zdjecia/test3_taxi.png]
	
	\caption{Wyznaczona ścieżka, metryka miejska}
\end{figure}

\subsubsection{Dystans oktalny}
Ostatnie sprawdzona heurestyka implementuje dystans oktalny opisany wzorem nr. \eqref{Eq:heuresticOctileDistance}
\begin{figure}[H]
	\centering
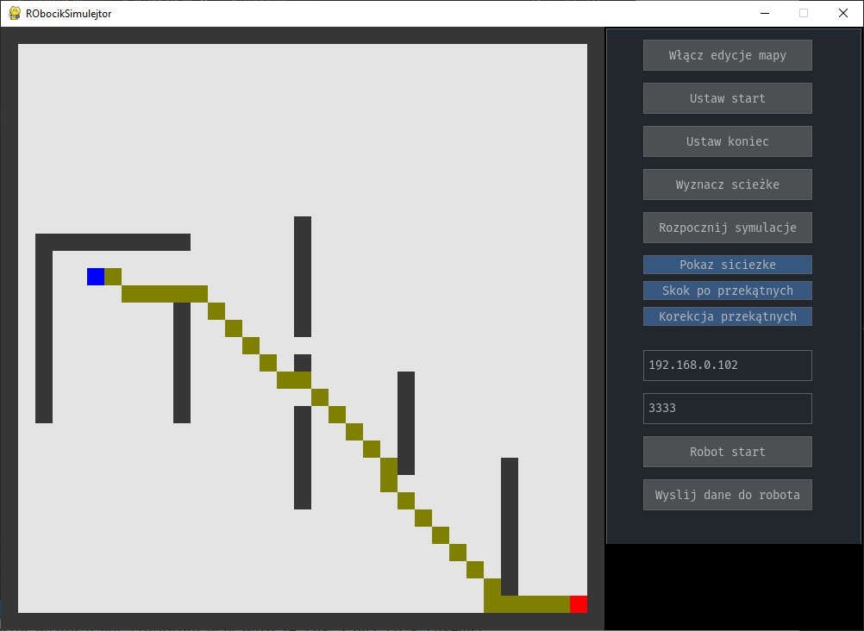
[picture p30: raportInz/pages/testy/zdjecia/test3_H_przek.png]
	
	\caption{Wyznaczona ścieżka, dystans oktalny}
\end{figure}

Jak widać na powyższych zrzutach ekranu funkcje heurestyczne mają bardzo duży wpływ na wygenerowaną trasę i jej wybór może być 
uzależniony od środowiska, w którym porusza się robot. W tym przypadku funkcja Eukalidesowa ze wzmocnieniem 1.41 jest optymalna, 
generuję najkrótszą ścieżkę z długimi prostymi odcinkami co w przypadku realnego robota przyśpieszy przejazd.

\subsection{Test komunikacji z fizycznym robotem}
Poniższy test ma na celu sprawdzenie komunikacji pomiędzy zbudowanym robotem a programem do sterowania. 
Aby przeprowadzić test, został napisany prosty graficzny program pozwalający na ręczne sterowanie robotem. 
Po za nim istnieje konsola z możliwością wprowadzania i wysyłania komend.
W pierwszej kolejności należy poznać adres sieciowy jaki robot dostał od serwera DHCP. Aby to zrobić 
należy podłączyć mikrkontroler do komputera poprzez kabel usb i zainstalowaną przejściówkę USB-UART. 
Po uruchomieniu monitora odczytującego dane ze wskazanego portu, można odczytać adres. 
\begin{figure}[H]
	\centering
	
	\caption{Odczytany adres IP}
\end{figure}
W następnym kroku możemy połączyć się przy pomocy konsoli lub dedykowanego programu. 
\begin{figure}[H]
	\centering
	
	\caption{Testowe połączenie z konsoli}
\end{figure}

\begin{figure}[H]
	\centering
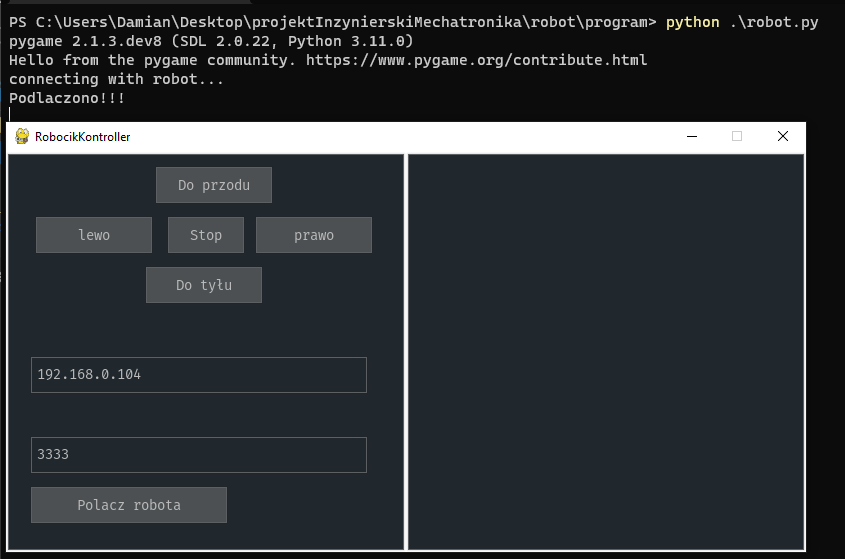
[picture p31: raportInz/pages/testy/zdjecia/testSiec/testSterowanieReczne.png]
	
	\caption{Testowe połączenie do sterowania ręcznego}
\end{figure}

Po połączeniu z robotem możliwe jest ręczne sterowanie przy pomocy dedykowanych przycisków lub klawisze w,s,a i d.
Jeżeli wprowadzony adres ip jest błędny, w konsoli pojawi się odpowiedni komunikat opisujący błąd.

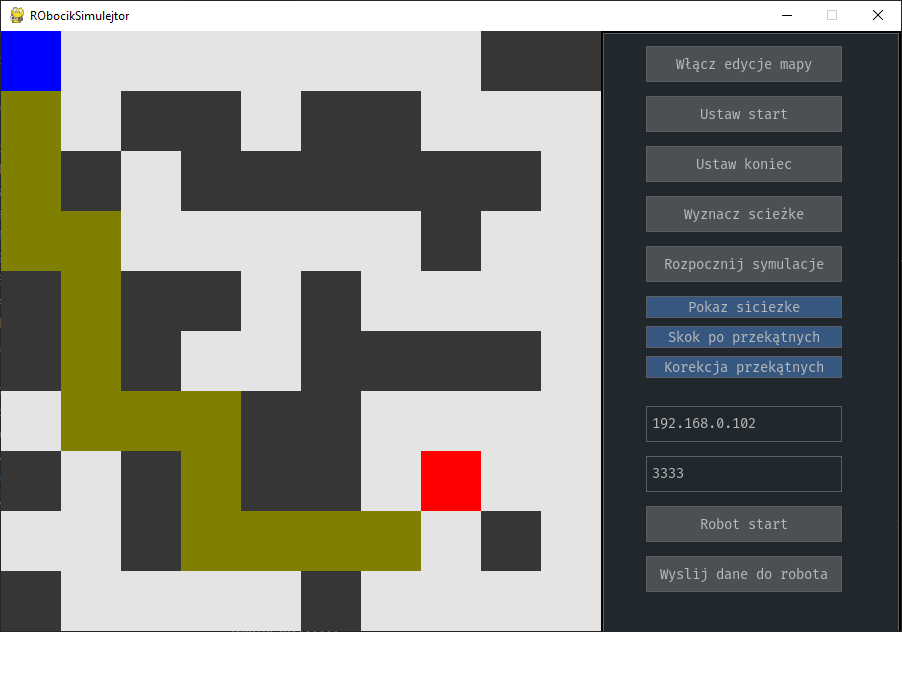
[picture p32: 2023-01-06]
raportInz/pages/testy/zdjecia/t1_1.png

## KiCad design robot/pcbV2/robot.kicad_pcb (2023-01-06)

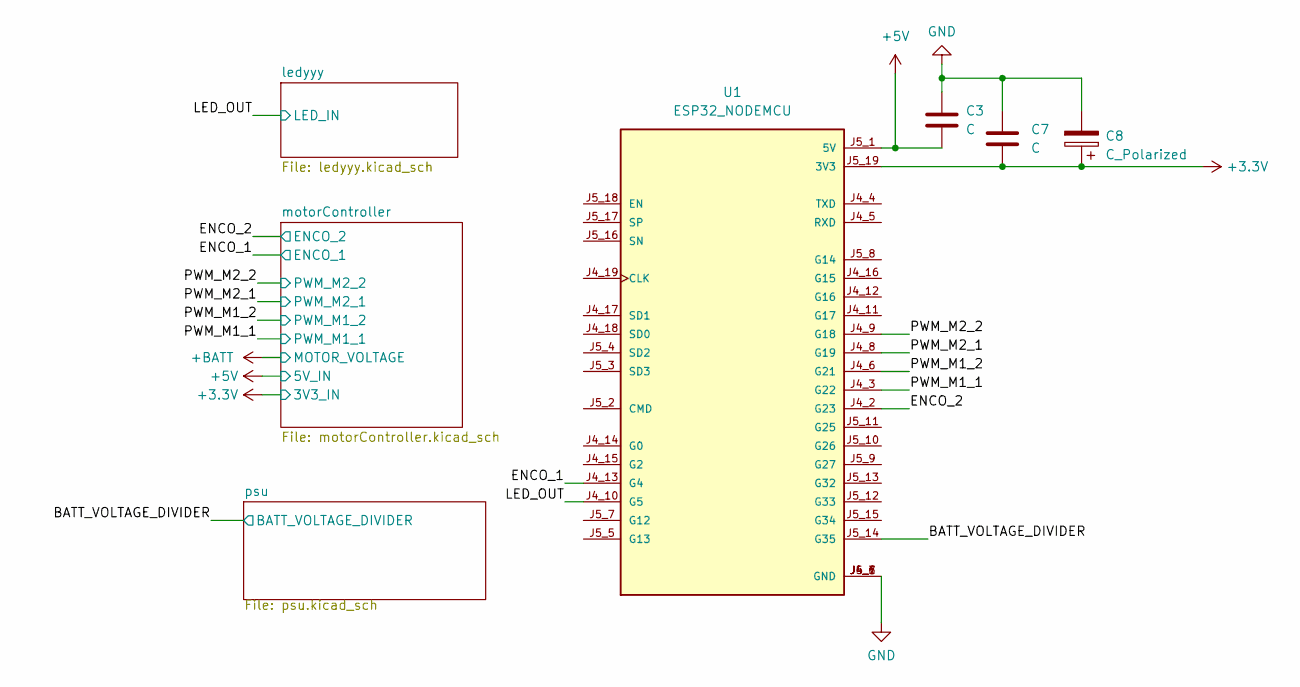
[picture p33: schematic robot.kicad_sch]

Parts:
C3, C7: C; C_1210_3225Metric
C8: C_Polarized; CP_Elec_6.3x7.7
U1: ESP32_NODEMCU; MODULE_ESP32_NODEMCU

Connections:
+3.3V: C7.2, C8.1, U1.J5_19 (3V3); also elsewhere on the board
+5V: C3.2, U1.J5_1 (5V); also elsewhere on the board
-BATT: C3.1, C7.1, C8.2, U1.J4_1 (GND), U1.J4_7 (GND), U1.J5_6 (GND); also elsewhere on the board
/BATT_VOLTAGE_DIVIDER: U1.J5_14 (G35); also elsewhere on the board
/ENCO_1: U1.J4_13 (G4); also elsewhere on the board
/ENCO_2: U1.J4_2 (G23); also elsewhere on the board
/LED_OUT: U1.J4_10 (G5); also elsewhere on the board
/PWM_M1_1: U1.J4_3 (G22); also elsewhere on the board
/PWM_M1_2: U1.J4_6 (G21); also elsewhere on the board
/PWM_M2_1: U1.J4_8 (G19); also elsewhere on the board
/PWM_M2_2: U1.J4_9 (G18); also elsewhere on the board

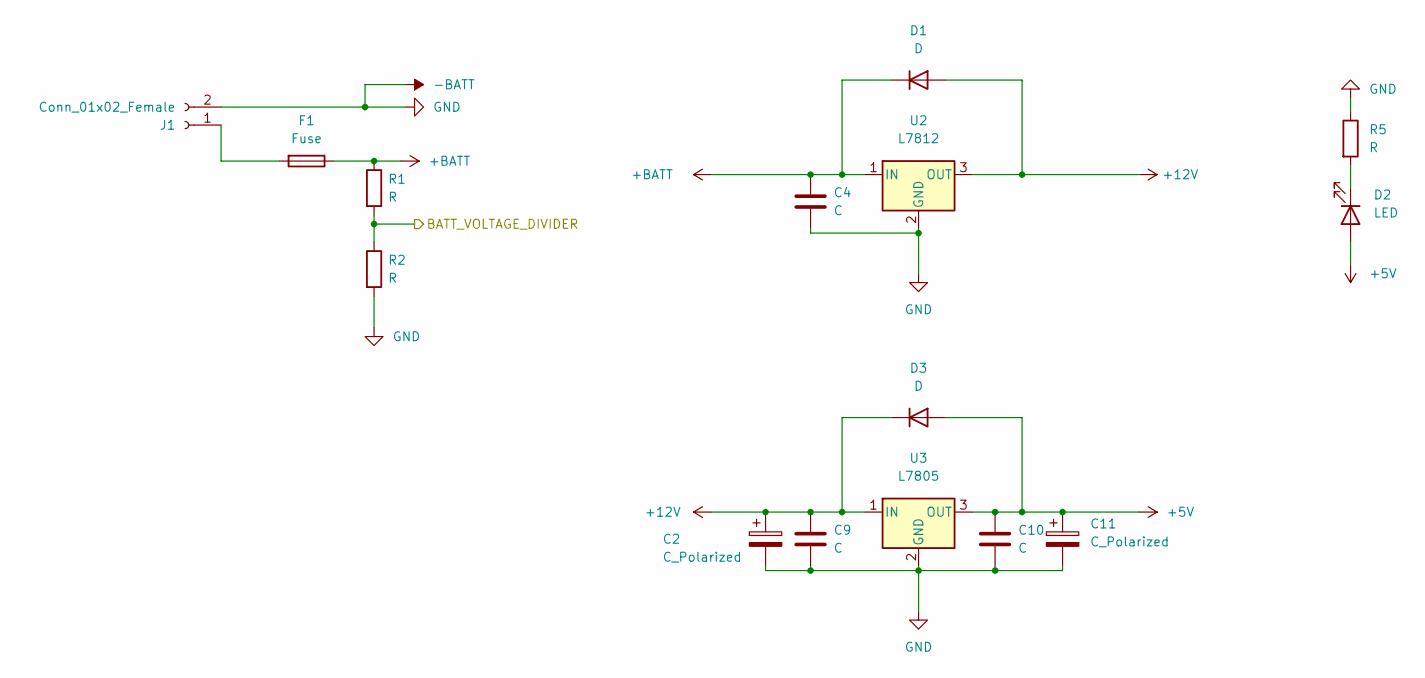
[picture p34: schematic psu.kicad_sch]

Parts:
C2, C11: C_Polarized; CP_Elec_6.3x7.7
C4, C9, C10: C; C_1210_3225Metric
D1, D3: D; D_1210_3225Metric
D2: LED; LED_D3.0mm
F1: Fuse; Fuse_1210_3225Metric_Pad1.42x2.65mm_HandSolder
J1: Conn_01x02_Female; TerminalBlock_bornier-2_P5.08mm
R1, R2, R5: R; R_Axial_DIN0207_L6.3mm_D2.5mm_P10.16mm_Horizontal
U2: L7812; TO-220-3_Vertical
U3: L7805; TO-252-2

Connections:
+5V: C10.1, C11.1, D2.2 (A), D3.2 (A), U3.3 (OUT); also elsewhere on the board
+12V: C2.1, C9.1, D1.2 (A), D3.1 (K), U2.3 (OUT), U3.1 (IN)
+BATT: C4.1, D1.1 (K), F1.1, R1.1, U2.1 (IN); also elsewhere on the board
-BATT: C2.2, C4.2, C9.2, C10.2, C11.2, J1.2, R2.2, R5.1, U2.2 (GND), U3.2 (GND); also elsewhere on the board
/BATT_VOLTAGE_DIVIDER: R1.2, R2.1; also elsewhere on the board
unnamed: D2.1 (K), R5.2
unnamed: F1.2, J1.1

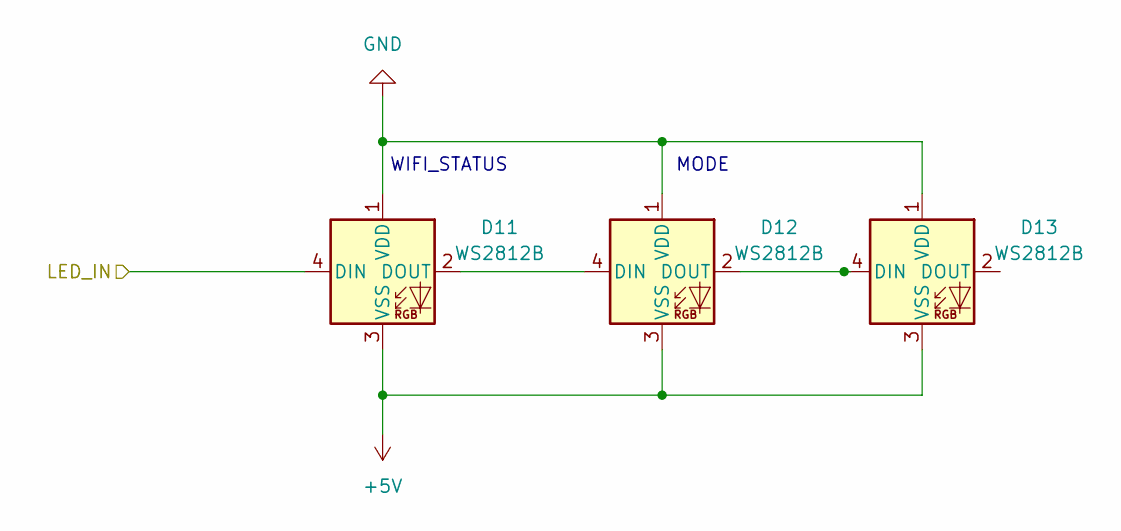
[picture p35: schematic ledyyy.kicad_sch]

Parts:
D11, D12, D13: WS2812B; LED_WS2812B_PLCC4_5.0x5.0mm_P3.2mm

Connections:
+5V: D11.3 (VSS), D12.3 (VSS), D13.3 (VSS); also elsewhere on the board
-BATT: D11.1 (VDD), D12.1 (VDD), D13.1 (VDD); also elsewhere on the board
/LED_OUT: D11.4 (DIN); also elsewhere on the board
unnamed: D11.2 (DOUT), D12.4 (DIN)
unnamed: D12.2 (DOUT), D13.4 (DIN)

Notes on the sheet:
WIFI_STATUS
MODE

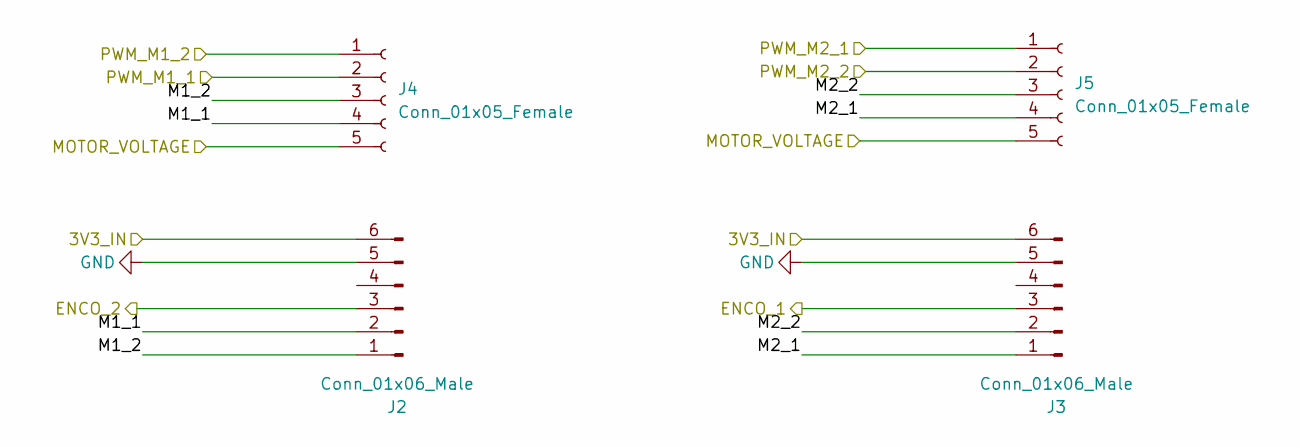
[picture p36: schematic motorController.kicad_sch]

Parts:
J2, J3: Conn_01x06_Male; Hirose_DF13C_CL535-0406-3-51_1x06-1MP_P1.25mm_Vertical
J4, J5: Conn_01x05_Female; SolderWire-0.75sqmm_1x05_P4.8mm_D1.25mm_OD2.3mm

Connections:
+3.3V: J2.6, J3.6; also elsewhere on the board
+BATT: J4.5, J5.5; also elsewhere on the board
-BATT: J2.5, J3.5; also elsewhere on the board
/ENCO_1: J3.3; also elsewhere on the board
/ENCO_2: J2.3; also elsewhere on the board
/PWM_M1_1: J4.2; also elsewhere on the board
/PWM_M1_2: J4.1; also elsewhere on the board
/PWM_M2_1: J5.1; also elsewhere on the board
/PWM_M2_2: J5.2; also elsewhere on the board
/motorController/M1_1: J2.2, J4.4
/motorController/M1_2: J2.1, J4.3
/motorController/M2_1: J3.1, J5.4
/motorController/M2_2: J3.2, J5.3

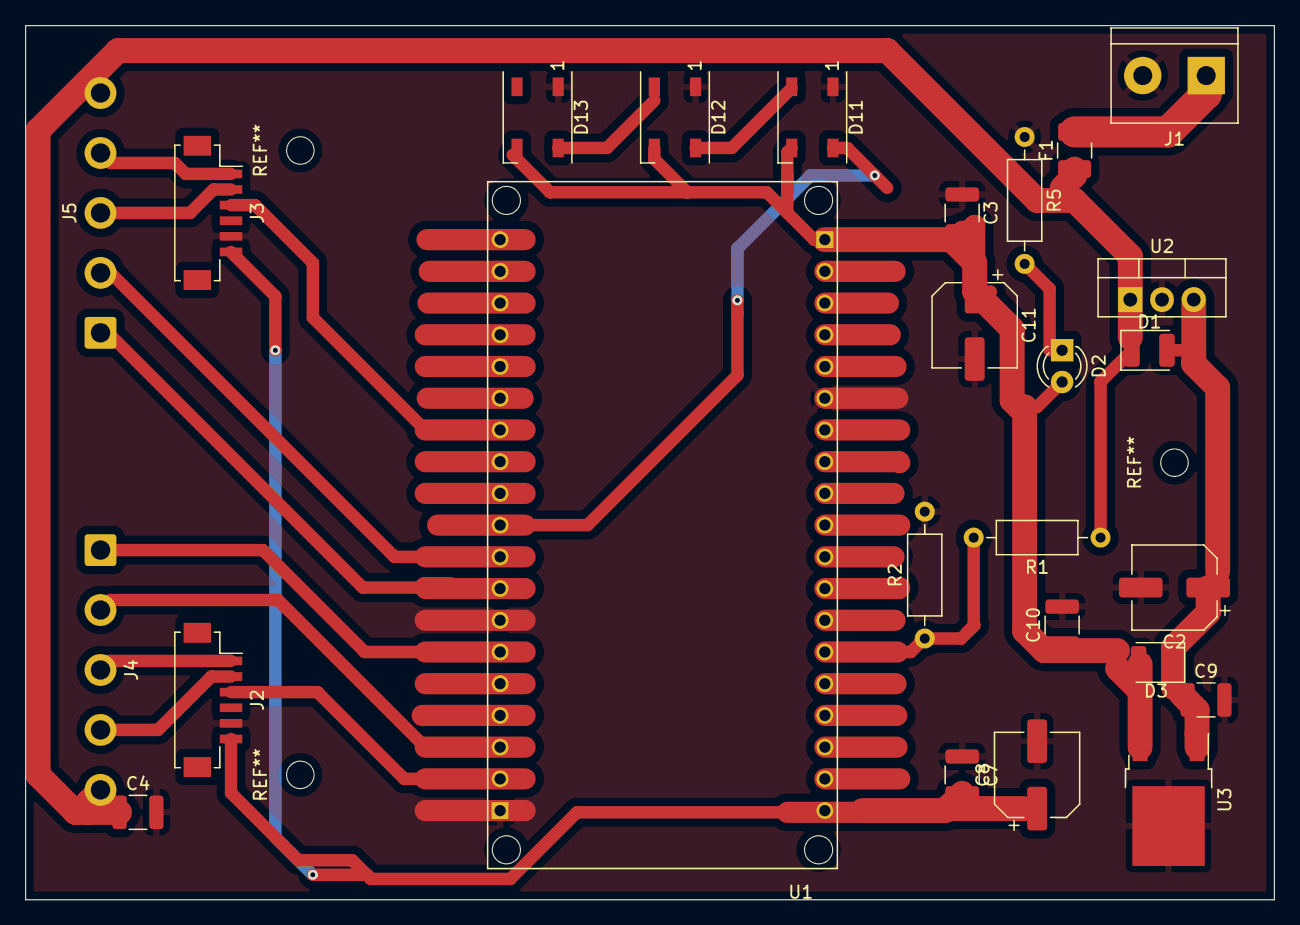
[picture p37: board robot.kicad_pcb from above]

Board: 2 copper layers, 100.0 x 70.0 mm, 26 parts (0 on the bottom side), 21 nets.

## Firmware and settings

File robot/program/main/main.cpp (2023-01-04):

#include "freertos/FreeRTOS.h"
#include "freertos/task.h"
#include "freertos/event_groups.h"
#include "esp_wifi.h"
#include "esp_event.h"
#include "esp_log.h"
#include "asio.hpp"
#include "esp_timer.h"
#include <math.h>

#include "WiFiConnection.hpp"
#include "server.hpp"
#include "System.hpp"

extern "C" 
{
   void app_main(void);
}

void app_main(void)
{
   const char* TAG = "SYSTEM";
   const short PORT = 3333;

   System& sys = System::getInstance();
   ESP_LOGI(TAG, "Inicjalizacja systemu");
   sys.initFileSystem();
   sys.initLedCDriver();
   sys.initEngines();

   WiFiConnection& wifi = WiFiConnection::instance();
   {
      char ssids[3][20] = {"wifi2", "Wifis9", "900/2100/2"};
      char passs[3][20] = {"iubppac46eze", "zaq1@WSX", "ppp123abcAyA"};
      int connectionCount = 0;

      while(!wifi.isConnected() && connectionCount < 3)
      {
         wifi.connect(ssids[connectionCount], passs[connectionCount]);
         connectionCount++;
         vTaskDelay(1000/portTICK_PERIOD_MS);
      }
      if(!wifi.isConnected())
      {
         ESP_LOGE(TAG, "nie mozna polaczyc sie z siecia wifi!!");
         ESP_LOGE(TAG, "Restart za 5 sekund");
         for(int i = 0; i < 5; i++)
         {
            printf(".");
            vTaskDelay(1000/portTICK_PERIOD_MS);
         }
         esp_restart();
      }
   }

   ESP_LOGI(TAG, "Uruchamianie kontekstu ASIO");
   ESP_LOGI(TAG, "Uruchamianie serwera tcp na porcie: %i", PORT);
   asio::io_context io_context;
   server s(io_context, PORT);
   xTaskCreatePinnedToCore([](void* ptr) -> void {
      ((asio::io_context*)ptr)->run();
   }, "tcp_server", 4096, &io_context, 30, NULL, 1);

   xTaskCreatePinnedToCore([] (void*ptr) -> void{
      gpio_config_t pinEncoderConfig;
      memset(&pinEncoderConfig, 0, sizeof(gpio_config_t));
      pinEncoderConfig.intr_type       = gpio_int_type_t::GPIO_INTR_DISABLE;
      pinEncoderConfig.mode            = gpio_mode_t::GPIO_MODE_INPUT_OUTPUT;
      pinEncoderConfig.pin_bit_mask    = ((1 << (int)gpio_num_t::GPIO_NUM_2));
      pinEncoderConfig.pull_up_en      = GPIO_PULLUP_DISABLE;
      pinEncoderConfig.pull_down_en    = GPIO_PULLDOWN_DISABLE;
      gpio_config(&pinEncoderConfig);
      while(1)
      {
         gpio_set_level(gpio_num_t::GPIO_NUM_2, !gpio_get_level(gpio_num_t::GPIO_NUM_2));
         vTaskDelay(800/portTICK_PERIOD_MS);
      }
   }, "LED_Blink_Task", 4096, NULL, 5, NULL, 1);


   while(true)
   {
      switch (sys.getRobotMode())
      {
         case RobotMode::ROBOT_MANUAL:
            switch (sys._manRobotDir)
            {
            case RobotDirection::DIR_FORWARD:
               sys.robotForward();
               break;
            case RobotDirection::DIR_BACKWARD:
               sys.robotBackward();
               break;
            case RobotDirection::DIR_LEFT:
               sys.robotRotateLeft();
               break;
            case RobotDirection::DIR_RIGHT:
               sys.robotRotateRight();
               break;
            default:
               sys.robotStop();
               break;
            }
         break;
         case RobotMode::ROBOT_AUTO:
            // if robot is in full path and run mode 
            // get next node from quuee
            // pid controller for absolute distance
            // if quuee is empty you reached goal
         break;
      }
      vTaskDelay(100 / portTICK_PERIOD_MS);   // just to keep the watchdog happy
   }
}

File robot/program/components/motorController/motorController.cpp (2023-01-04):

#include "motorController.hpp"


MotorController::MotorController(
    gpio_num_t pinIn1, gpio_num_t pinIn2, 
    gpio_num_t encoderPin, ledc_channel_t ledcChanel1,
    ledc_channel_t ledcChanel2)

    :PIDController(8, 0.1, 0.1, TIMER_CLEAR),
    _encoderTicks(0),_absoluteEncoderTicks(0),
    _engineRadialSpeed(0.0f), _currentRadialEngineSpeed(0.0f)
{
    this->_chanels[0] = ledcChanel1;
    this->_chanels[1] = ledcChanel2;

    // konfiguracja przerwania enkodera, programowo można zastąpić licznikiem esp32
    gpio_config_t pinEncoderConfig;
    memset(&pinEncoderConfig, 0, sizeof(gpio_config_t));
    pinEncoderConfig.intr_type       = GPIO_INTR_NEGEDGE;
    pinEncoderConfig.mode            = GPIO_MODE_INPUT;
    pinEncoderConfig.pin_bit_mask    = ((1 << (int)encoderPin));
    pinEncoderConfig.pull_up_en      = GPIO_PULLUP_DISABLE;
    pinEncoderConfig.pull_down_en    = GPIO_PULLDOWN_DISABLE;

    gpio_config(&pinEncoderConfig);
    gpio_install_isr_service(ESP_INTR_FLAG_LEVEL1);   
    gpio_isr_handler_add(encoderPin, MotorController::encoderInteruptHandler, this);

    this->_updater = xTimerCreate("encoTimer", pdMS_TO_TICKS(TIMER_CLEAR), pdTRUE, (void*)this, MotorController::clearEncoderTimer);
    xTimerStart(this->_updater, 0);

    // motor controlPins configuration
    ledc_channel_config_t motor_first_channel;
    motor_first_channel.speed_mode          = LEDC_LOW_SPEED_MODE;
    motor_first_channel.channel             = ledcChanel1;
    motor_first_channel.timer_sel           = LEDC_TIMER_0;
    motor_first_channel.intr_type           = LEDC_INTR_DISABLE;
    motor_first_channel.gpio_num            = (pinIn1); // output pin
    motor_first_channel.duty                = 0; // Set duty to 0%
    motor_first_channel.hpoint              = 0;
    motor_first_channel.flags.output_invert = 1;
    ESP_ERROR_CHECK(ledc_channel_config(&motor_first_channel));

    ledc_channel_config_t motor_second_channel;
    motor_second_channel.speed_mode             = LEDC_LOW_SPEED_MODE;
    motor_second_channel.channel                = ledcChanel2;
    motor_second_channel.timer_sel              = LEDC_TIMER_0;
    motor_second_channel.intr_type              = LEDC_INTR_DISABLE;
    motor_second_channel.gpio_num               = (pinIn2); // output pin
    motor_second_channel.duty                   = 0; // Set duty to 0%
    motor_second_channel.hpoint                 = 0;
    motor_second_channel.flags.output_invert    = 1;
    ESP_ERROR_CHECK(ledc_channel_config(&motor_second_channel));
}
MotorController::~MotorController()
{
    xTimerStop(this->_updater, 0);
}
void MotorController::update()
{
    // regulator pid bazuje na prędkości silnika
    // prędkosc kola jest przeliczana

    float setSpeed  = this->getEngineRadialSpeed();
    int pidToPwm    = 0;
    int pwmCh       = 0; // kanal ledc na ktory ma isc pwm

    if(abs(setSpeed) - 1 > 0) // jezeli predkosc jest wieksza to pid jak nie to hamulec bo pwm=0
    {
        pidToPwm = (int) this->calcOutput(abs(this->getCalculatedEngineRadialSpeed()), abs(setSpeed));
        if(setSpeed < 0)
        {
            // pidToPwm *= -1; // odwrocenie nastaw pid jezeli predkosc ujemna 
            pwmCh = 1;
        }
        else
            pwmCh = 0;

        pidToPwm += ledc_get_duty(LEDC_LOW_SPEED_MODE, this->_chanels[pwmCh]);
        pidToPwm = std::min(pidToPwm, 8192);
        pidToPwm = std::max(pidToPwm, 0);
    }

    // ustawienie wyjsc
    ledc_set_duty(LEDC_LOW_SPEED_MODE, this->_chanels[pwmCh], (int)pidToPwm);
    ledc_update_duty(LEDC_LOW_SPEED_MODE, this->_chanels[pwmCh]);

    // ustawienie drugiego kanalu
    ledc_set_duty(LEDC_LOW_SPEED_MODE, this->_chanels[(pwmCh==0)?1:0], 0);
    ledc_update_duty(LEDC_LOW_SPEED_MODE, this->_chanels[(pwmCh==0)?1:0]);
}
void MotorController::encoderInteruptHandler(void* _this)
{
    MotorController *t = (MotorController*) _this;
    t->_encoderTicks++;
    t->_absoluteEncoderTicks++;
}
void MotorController::clearEncoderTimer(TimerHandle_t xTimer)
{
    MotorController* t = (MotorController*) pvTimerGetTimerID(xTimer);
    float omega = (float)(2 * M_PI * t->_encoderTicks) / (float)(TICKS_PER_ROTATION * ((float)(TIMER_CLEAR)/1000)); 
    
    // czyszczenie licznika enkodera
    t->clearEncoder();
    
    if(t->_engineRadialSpeed < 0) omega*=-1; // jezeli nastawa na - to silnik obraca sie przeciwnie
    t->_currentRadialEngineSpeed = omega;

    // aktulizacja nastaw silnika
    t->update();

}
void MotorController::clearEncoder()
{
    this->_encoderTicks = 0;
}
void MotorController::setEngineRadialSpeed(float speed)
{
    this->_engineRadialSpeed = speed;
}
void MotorController::setWheelRadialSpeed(float speed)
{
    this->_engineRadialSpeed = speed/MotorController::GEAR_RATIO;
}
int MotorController::getEncoder() const 
{
    return this->_encoderTicks;
}
int MotorController::getAbsoluteEncoder() const 
{
    return this->_absoluteEncoderTicks;
}
float MotorController::getEngineRadialSpeed() const
{
    return this->_engineRadialSpeed;
}
float MotorController::getCalculatedEngineRadialSpeed() const
{
    // rad / s
    return this->_currentRadialEngineSpeed;
}
float MotorController::getWheelRadialSpeed() const
{
    // cm / s
    return this->_currentRadialEngineSpeed / MotorController::GEAR_RATIO;
}
float MotorController::getCalculatedWheelRadialSpeed() const
{
    // cm / s
    return this->_currentRadialEngineSpeed / MotorController::GEAR_RATIO;
}
float MotorController::getCurrentLinearDistance() const
{
    return (float)this->_currentRadialEngineSpeed / ((float)TIMER_CLEAR * 0.001);
}
float MotorController::getAbsoluteLinearDistance() const
{
    return ((float)this->_absoluteEncoderTicks / (float)MotorController::TICKS_PER_ROTATION_LARGE) * MotorController::TIRE_RADIUS;
}

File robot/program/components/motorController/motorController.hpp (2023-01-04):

#include <iostream>
#include <stdio.h>
#include <cstring>
#include <math.h>

#include <freertos/freertos.h>
#include <freertos/timers.h>
#include <driver/gpio.h>
#include "driver/ledc.h"
#include "esp_log.h"

#include "PIDController.hpp"

/*
    units:
        for ratations   -> rad / s
        for linera      -> cm / s

*/
class MotorController :protected PIDController
{
public:
    MotorController(gpio_num_t pinIn1, gpio_num_t pinIn2,
    gpio_num_t encoerPin, ledc_channel_t ledcChanel1, 
    ledc_channel_t ledcChanel2);

    ~MotorController();

    void clearEncoder();
    void setEngineRadialSpeed(float speed);
    void setWheelRadialSpeed(float speed);

    int getEncoder()                        const;
    int getAbsoluteEncoder()                const;

    float getEngineRadialSpeed()            const;
    float getCalculatedEngineRadialSpeed()  const;

    float getWheelRadialSpeed()             const;
    float getCalculatedWheelRadialSpeed()   const;

    float getCurrentLinearDistance()        const;
    float getAbsoluteLinearDistance()       const;

    static void encoderInteruptHandler(void*);
    static void clearEncoderTimer(TimerHandle_t);

    static const int MIN_PWM_VAL                = 0;
    static const int MAX_PWM_VAL                = 8192;

    static const int TIMER_CLEAR                = 100;       //ms
    static const int TICKS_PER_ROTATION         = 14;       
    static const int TICKS_PER_ROTATION_LARGE   = 700;
    static constexpr float TIRE_RADIUS         = (6.4/2);   // cm
    static constexpr float GEAR_RATIO          = 0.02;
protected:
    void update();

    int _encoderTicks, _absoluteEncoderTicks;
    float _engineRadialSpeed, _currentRadialEngineSpeed;
    
    TimerHandle_t _updater;
    ledc_channel_t _chanels[2];
};

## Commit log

2022-11-28 ver 0.5
    [Nowy Arkusz programu Microsoft Excel.xlsx, ledyyy.kicad_sch, motorController.kicad_sch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]
2023-01-04 dopisany tekst w latexie
    [robot.kicad_pcb, robot.kicad_sch]
2023-01-04 przeniesienie folderow
    [Nowy Arkusz programu Microsoft Excel.xlsx]
2023-01-04 kopia kicad
2023-01-06 aktulizacja .gitignore
    [ledyyy.kicad_sch, motorController.kicad_sch, psu.kicad_sch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]
2023-01-10 zmienieony opis elektroniki i modelu, uproszczone schematy w kicadzie
2023-01-10 uproszczony schemat
    [robot.kicad_sch]
2023-01-18 cad robota
    [robotCad.f3z]
